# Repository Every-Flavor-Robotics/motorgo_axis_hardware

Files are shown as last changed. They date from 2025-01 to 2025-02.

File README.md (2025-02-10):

# MotorGo AXIS
## The aim of this project is to integrate a dual bldc motor controller with an ESP32 AND make it piHat compatible for the rpi 4 and 5
### Schematics and Layouts and Renders: 
(This is a first pass draft, so be patient with my formatting and content)

- Full board 3D:


- Top level


- Motor drivers 


- IMU 


- Power system 


- connectors 


- Dimensions 


## Demo
This is still in testing, but already at this state, it is capable of making 2 axis gantry robots quite easily.  Check out this project we made with it while developing the motor controller:
https://www.youtube.com/watch?v=p4cUWCG7fM4

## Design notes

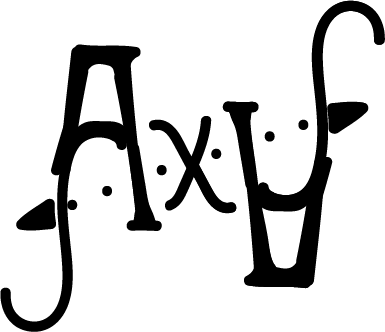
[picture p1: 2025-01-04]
graphics/1x/AxisArt.png

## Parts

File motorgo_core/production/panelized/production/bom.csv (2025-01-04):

Designator | Footprint | Quantity | Value | LCSC Part #
C1_3, C1_2, C1 | 0201 | 3 | 68pf 10v
C10_3, C10_2, C10, C11_3, C11_2, C11, C12_3, C12_2, C12, C13_3, C13_2, C13, C14_3, C14_2, C14, C21_3, C21_2, C21, C27_3, C27_2, C27, C28_3, C28_2, C28, C35_3, C35_2, C35, C36_3, C36_2, C36, C37_3, C37_2, C37, C38_3, C38_2, C38, C40_3, C40_2, C40, C41_3, C41_2, C41, C42_3, C42_2, C42, C43_3, C43_2, C43, C44_3, C44_2, C44, C45_3, C45_2, C45, C47_3, C47_2, C47, C48_3, C48_2, C48, C5_3, C5_2, C5, C6_3, C6_2, C6, C7_3, C7_2, C7, C8_3, C8_2, C8 | 0402 | 72 | 22uF 10v
C15_3, C15_2, C15, C2_3, C2_2, C2 | 0805 | 6 | 4.7uF 1mOhm 25v
C16_3, C16_2, C16 | CP_Elec_10x10.5 | 3 | 470uF 35V
C17_3, C17_2, C17 | 0603 | 3 | 4.7uF 1mOhm
C18_3, C18_2, C18 | 0201 | 3 | 2.2nF 0Ohm
C19_3, C19_2, C19 | 0805 | 3 | 4.7uF 1mOhm
C20_3, C20_2, C20 | 0201 | 3 | 6.8nf 10v
C22_3, C22_2, C22 | 0402 | 3 | 100nf 280mOhm
C23_3, C23_2, C23 | 1210 | 3 | 47uF 3mOhm 25v
C24_3, C24_2, C24, C25_3, C25_2, C25 | 0603 | 6 | 22uF 16v
C26_3, C26_2, C26, C30_3, C30_2, C30, C31_3, C31_2, C31, C34_3, C34_2, C34, C39_3, C39_2, C39, C4_3, C4_2, C4, C46_3, C46_2, C46, C9_3, C9_2, C9 | 0201 | 24 | 100nF 10v
C3_3, C3_2, C3, C33_3, C33_2, C33 | 0201 | 6 | 100nF 25v
C32_3, C32_2, C32 | 0603 | 3 | 1uF 10v
D1_3, D1_2, D1 | 0805 | 3 | LED blue
D10_3, D10_2, D10, D5_3, D5_2, D5, D6_3, D6_2, D6, D7_3, D7_2, D7, D8_3, D8_2, D8, D9_3, D9_2, D9 | B5819WS_SOD-323 | 18 | D_Schottky C7420331
D2_3, D2_2, D2 | 0805 | 3 | LED green
D3_3, D3_2, D3 | 0805 | 3 | LED red
D4_3, D4_2, D4 | TO-277_3P-L5.4-W4.0-LS6.5-TR | 3 | Schottky_SB1045L_C908747
J1_3, J1_2, J1 | USB-C-SMD_TYPEC-303-ACP16 | 3 | USB4520-03-0-A_REVA
J11_3, J11_2, J11 | CONN-TH_XT30PW-M | 3 | xt30
J13_3, J13_2, J13, J15_3, J15_2, J15 | JST_SH_BM04B-SRSS-TB_1x04-1MP_P1.00mm_Vertical | 6 | I2C_STANDARDQWIIC
J16_3, J16_2, J16, J18_3, J18_2, J18 | JST_SH_BM05B-SRSS-TB_1x05-1MP_P1.00mm_Vertical | 6 | BM05B-SRSS-TB_LF__SN_
J2_3, J2_2, J2, J3_3, J3_2, J3 | SW_SPST_TL3342 | 6 | C2886897
J4_3, J4_2, J4, J7_3, J7_2, J7 | PinSocket_2x20_P2.54mm_Vertical_SMD | 6 | Conn_02x20_Odd_Even
KIKIT_FID_B_1, KIKIT_FID_B_2, KIKIT_FID_B_3, KIKIT_FID_B_4, KIKIT_FID_T_1, KIKIT_FID_T_2, KIKIT_FID_T_3, KIKIT_FID_T_4 | Fiducial | 8 | Fiducial
KIKIT_TO_1, KIKIT_TO_2, KIKIT_TO_3, KIKIT_TO_4 | NPTH | 4 | NPTH
L1_3, L1_2, L1 | IND-SMD_L6.6-W6.4_CKSTT0610 | 3 | 2.2uH 12.7mOhm C5440776
Q1_3, Q1_2, Q1, Q10_3, Q10_2, Q10, Q11_3, Q11_2, Q11, Q12_3, Q12_2, Q12, Q2_3, Q2_2, Q2, Q3_3, Q3_2, Q3, Q4_3, Q4_2, Q4, Q5_3, Q5_2, Q5, Q6_3, Q6_2, Q6, Q7_3, Q7_2, Q7, Q8_3, Q8_2, Q8, Q9_3, Q9_2, Q9 | AP30H80Q_DFN-8 | 36 | AP30H80Q
R1_3, R1_2, R1, R2_3, R2_2, R2, R3_3, R3_2, R3, R46_3, R46_2, R46, R49_3, R49_2, R49, R50_3, R50_2, R50 | 0402 | 18 | 1k
R10_3, R10_2, R10, R11_3, R11_2, R11, R12_3, R12_2, R12, R13_3, R13_2, R13, R14_3, R14_2, R14, R15_3, R15_2, R15, R20_3, R20_2, R20, R21_3, R21_2, R21, R22_3, R22_2, R22, R23_3, R23_2, R23, R26_3, R26_2, R26, R27_3, R27_2, R27 | 0402 | 36 | 2R2
R16_3, R16_2, R16 | 0402 | 3 | 102k
R17_3, R17_2, R17 | 0402 | 3 | 36.5k
R18_3, R18_2, R18, R24_3, R24_2, R24 | 0402 | 6 | 53.6k
R19_3, R19_2, R19 | 0402 | 3 | 3.92k
R25_3, R25_2, R25 | 0402 | 3 | 10k
R30_3, R30_2, R30, R31_3, R31_2, R31, R32_3, R32_2, R32, R33_3, R33_2, R33, R4_3, R4_2, R4, R5_3, R5_2, R5, R8_3, R8_2, R8, R9_3, R9_2, R9 | 0402 | 24 | 5k1
R38_3, R38_2, R38, R39_3, R39_2, R39 | 0402 | 6 | 2k
R6_3, R6_2, R6, R7_3, R7_2, R7 | 0402 | 6 | 0
U1_3, U1_2, U1 | ESP32-S3-WROOM-1 | 3 | ESP32-S3-WROOM-1
U10_3, U10_2, U10 | LIS3MDLTR_LGA-12 | 3 | LIS3MDLTR
U11_3, U11_2, U11 | LSM6DSOTR_LGA-14 | 3 | LSM6DS3TR
U2_3, U2_2, U2 | SOT-666 | 3 | USBLC6-2P6
U3_3, U3_2, U3, U4_3, U4_2, U4 | FD6288Q_QFN-24 | 6 | FD6288
U6_3, U6_2, U6 | VQFN-14_L3.5-W3.5-P0.50-TL-EP_TPS54622RHLT | 3 | TPS54620RHLR
U8_3, U8_2, U8 | SOT-223-3_TabPin2 | 3 | AMS1117-3.3

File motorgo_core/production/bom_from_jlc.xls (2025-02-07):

Comment | topDesignator | bottomDesignator | Footprint | JLCPCB Part #
22uF10v | C10_3,C10_2,C10,C11_3,C11_2,C11,C12_3,C12_2,C12,C13_3,C13_2,C13,C14_3,C14_2,C14,C21_3,C21_2,C21,C27_3,C27_2,C27,C28_3,C28_2,C28,C35_3,C35_2,C35,C36_3,C36_2,C36,C37_3,C37_2,C37,C38_3,C38_2,C38,C40_3,C40_2,C40,C41_3,C41_2,C41,C42_3,C42_2,C42,C43_3,C43_2,C43,C44_3,C44_2,C44,C45_3,C45_2,C45,C47_3,C47_2,C47,C48_3,C48_2,C48,C5_3,C5_2,C5,C6_3,C6_2,C6,C7_3,C7_2,C7,C8_3,C8_2,C8 |  | 0402 | C3845593
22uF16v | C24_3,C24_2,C24,C25_3,C25_2,C25 |  | 0603 | C2762594
68pf10v | C1_3,C1_2,C1 |  | 0201 | C277473
4.7uF1mOhm | C15_3,C15_2,C15,C2_3,C2_2,C2,C19_3,C19_2,C19 |  | 0805 | C1779
FD6288 | U3_3,U3_2,U3,U4_3,U4_2,U4 |  | FD6288Q_QFN-24 | C328453
47uF3mOhm25v | C23_3,C23_2,C23 |  | 1210 | C7432791
10k | R25_3,R25_2,R25 |  | 0402 | C25744
6.8nf10v | C20_3,C20_2,C20 |  | 0201 | C565541
36.5k | R17_3,R17_2,R17 |  | 0402 | C25887
AP30H80Q | Q1_3,Q1_2,Q1,Q10_3,Q10_2,Q10,Q11_3,Q11_2,Q11,Q12_3,Q12_2,Q12,Q2_3,Q2_2,Q2,Q3_3,Q3_2,Q3,Q4_3,Q4_2,Q4,Q5_3,Q5_2,Q5,Q6_3,Q6_2,Q6,Q7_3,Q7_2,Q7,Q8_3,Q8_2,Q8,Q9_3,Q9_2,Q9 |  | AP30H80Q_DFN-8 | C2828592
TPS54620RHLR | U6_3,U6_2,U6 |  | VQFN-14_L3.5-W3.5-P0.50-TL-EP_TPS54622RHLT | C263274
USBLC6-2P6 | U2_3,U2_2,U2 |  | SOT-666 | C2827693
xt30 | J11_3,J11_2,J11 |  | CONN-TH_XT30PW-M | C431092
LSM6DS3TR | U11_3,U11_2,U11 |  | LSM6DSOTR_LGA-14 | C95230
LEDblue | D1_3,D1_2,D1 |  | 0805 | C2293
C2886897 | J2_3,J2_2,J2,J3_3,J3_2,J3 |  | SW_SPST_TL3342 | C2886897
2.2nF0Ohm | C18_3,C18_2,C18 |  | 0201 | C161488
4.7uF1mOhm | C17_3,C17_2,C17 |  | 0603 | C19666
BM05B-SRSS-TB_LF__SN_ | J16_3,J16_2,J16,J18_3,J18_2,J18 |  | JST_SH_BM05B-SRSS-TB_1x05-1MP_P1.00mm_Vertical | C160391
ESP32-S3-WROOM-1 | U1_3,U1_2,U1 |  | ESP32-S3-WROOM-1 | C2913202
LEDgreen | D2_3,D2_2,D2 |  | 0805 | C2297
1k | R1_3,R1_2,R1,R2_3,R2_2,R2,R3_3,R3_2,R3,R46_3,R46_2,R46,R49_3,R49_2,R49,R50_3,R50_2,R50 |  | 0402 | C11702
LEDred | D3_3,D3_2,D3 |  | 0805 | C434431
2.2uH12.7mOhmC5440776 | L1_3,L1_2,L1 |  | IND-SMD_L6.6-W6.4_CKSTT0610 | C5440776
100nF25v | C26_3,C26_2,C26,C30_3,C30_2,C30,C31_3,C31_2,C31,C34_3,C34_2,C34,C39_3,C39_2,C39,C4_3,C4_2,C4,C46_3,C46_2,C46,C9_3,C9_2,C9,C3_3,C3_2,C3,C33_3,C33_2,C33 |  | 0201 | C76939
3.92k | R19_3,R19_2,R19 |  | 0402 | C137988
100nf280mOhm | C22_3,C22_2,C22 |  | 0402 | C1525
5k1 | R30_3,R30_2,R30,R31_3,R31_2,R31,R32_3,R32_2,R32,R33_3,R33_2,R33,R4_3,R4_2,R4,R5_3,R5_2,R5,R8_3,R8_2,R8,R9_3,R9_2,R9 |  | 0402 | C25905
2k | R38_3,R38_2,R38,R39_3,R39_2,R39 |  | 0402 | C4109
53.6k | R18_3,R18_2,R18,R24_3,R24_2,R24 |  | 0402 | C53398
USB4520-03-0-A_REVA | J1_3,J1_2,J1 |  | USB-C-SMD_TYPEC-303-ACP16 | C720628
Conn_02x20_Odd_Even | J4_3,J4_2,J4 | J7_3,J7_2,J7 | PinSocket_2x20_P2.54mm_Vertical_SMD | C3975165
D_SchottkyC7420331 | D10_3,D10_2,D10,D5_3,D5_2,D5,D6_3,D6_2,D6,D7_3,D7_2,D7,D8_3,D8_2,D8,D9_3,D9_2,D9 |  | B5819WS_SOD-323 | C7420331
102k | R16_3,R16_2,R16 |  | 0402 | C26991
LIS3MDLTR | U10_3,U10_2,U10 |  | LIS3MDLTR_LGA-12 | C478483
470uF35V | C16_3,C16_2,C16 |  | CP_Elec_10x10.5 | C2836436
0 | R6_3,R6_2,R6,R7_3,R7_2,R7 |  | 0402 | C17168
1uF10v | C32_3,C32_2,C32 |  | 0603 | C15849
AMS1117-3.3 | U8_3,U8_2,U8 |  | SOT-223-3_TabPin2 | C6186
I2C_STANDARDQWIIC | J13_3,J13_2,J13,J15_3,J15_2,J15 |  | JST_SH_BM04B-SRSS-TB_1x04-1MP_P1.00mm_Vertical | C160390
2R2 | R10_3,R10_2,R10,R11_3,R11_2,R11,R12_3,R12_2,R12,R13_3,R13_2,R13,R14_3,R14_2,R14,R15_3,R15_2,R15,R20_3,R20_2,R20,R21_3,R21_2,R21,R22_3,R22_2,R22,R23_3,R23_2,R23,R26_3,R26_2,R26,R27_3,R27_2,R27 |  | 0402 | C25158
Schottky_SB1045L_C908747 | D4_3,D4_2,D4 |  | TO-277_3P-L5.4-W4.0-LS6.5-TR | C908747

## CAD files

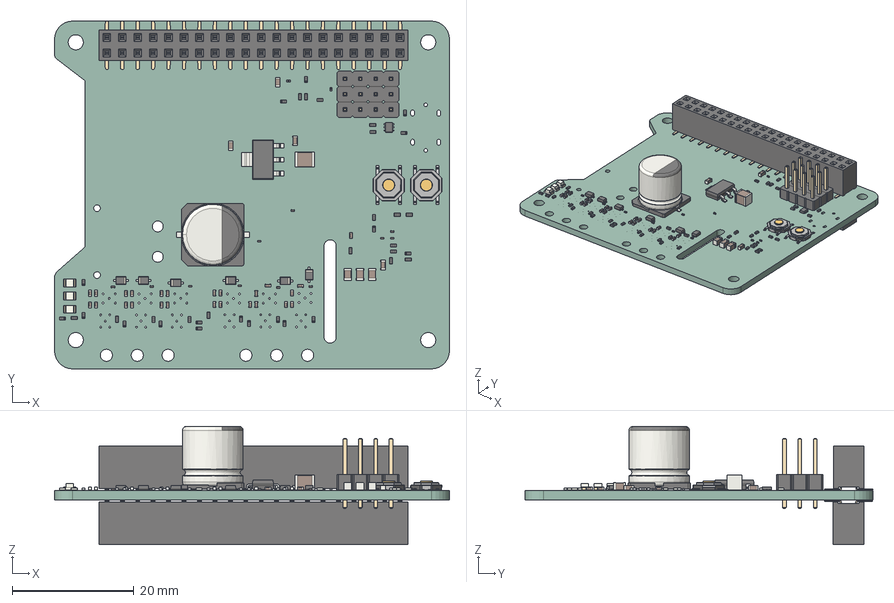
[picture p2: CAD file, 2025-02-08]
mg_axis.step
65.0 x 57.2 x 19.5 mm
C_0402_1005Metric x 25
C_0201_0603Metric x 13
R_0402_1005Metric x 36
D_SOD_323F x 6
SW_SPST_TL3342 x 2
C_0603_1608Metric x 4
PinHeader_1x04_P254mm_Vertical x 3
SOT_666
LED_0805_2012Metric x 3
C_0805_2012Metric x 3
CP_Elec_10x105
SOT_223
C_1210_3225Metric
PinSocket_2x20_P254mm_Vertical_SMD x 2
motorgo_core_PCB

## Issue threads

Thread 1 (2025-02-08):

3D model is missing parts

alexchunlin, 2025-02-08:
## Currently, the 3d STEP file of the board has the biggest components, like the board outline, the bulk capacitor, and the GPIO headers for the top and bottom of the board.

### HOWEVER it is still missing the following big components:
- esp32
- USBC port
- Qwiic ports
- Encoder ports
- XT30 Connector

### As wells as the following smaller components that people might care about:
- mosfets
- leds
- literally every SMD passive, but particularly the chonky inductor
- the IMU and Magnetometer

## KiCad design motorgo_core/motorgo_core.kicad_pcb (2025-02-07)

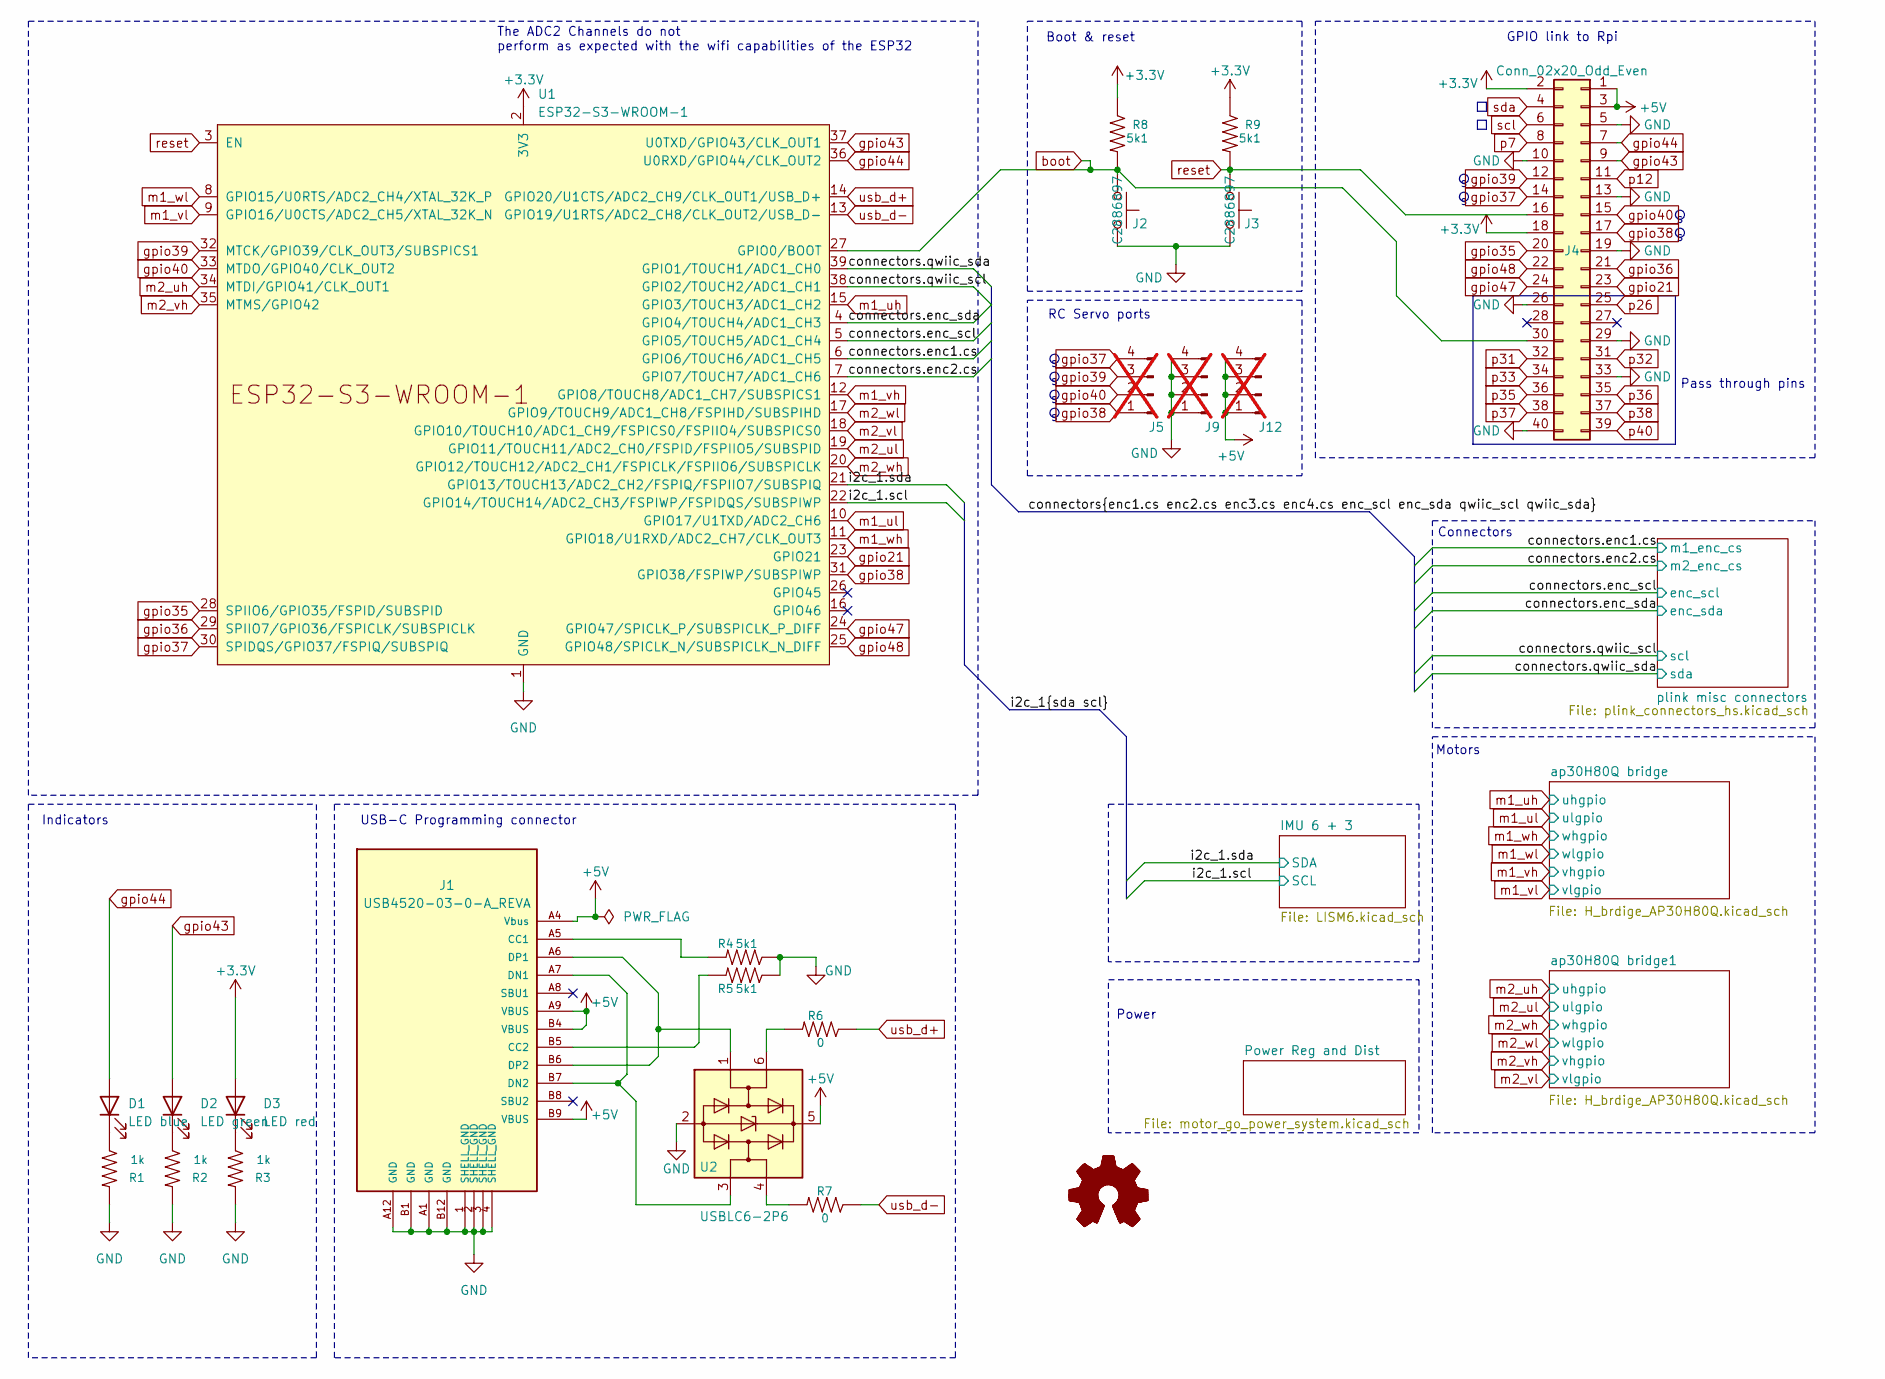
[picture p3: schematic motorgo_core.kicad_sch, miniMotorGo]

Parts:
D1: LED blue; LED_0805_2012Metric; LCSC_Part_Number C84259
D2: LED green; LED_0805_2012Metric; LCSC_Part_Number C84260
D3: LED red; LED_0805_2012Metric; LCSC_Part_Number C84256
J1: USB4520-03-0-A_REVA; USB-C-SMD_TYPEC-303-ACP16; LCSC_Part_Number C720628
J2, J3: C2886897; SW_SPST_TL3342; LCSC_Part_Number C2886897
J4: Conn_02x20_Odd_Even; PinSocket_2x20_P2.54mm_Vertical_SMD; LCSC_Part_Number C3975165
J5, J9, J12: Conn_01x04_Pin; PinHeader_1x04_P2.54mm_Vertical; not fitted
R1, R2, R3: 1k; R_0402_1005Metric; LCSC_Part_Number C11702
R4, R5, R8, R9: 5k1; R_0402_1005Metric; LCSC_Part_Number C25905
R6, R7: 0; R_0402_1005Metric; LCSC_Part_Number C3017451
U1: ESP32-S3-WROOM-1; LCSC_Part_Number C2913198
U2: USBLC6-2P6; SOT-666; LCSC_Part_Number C2827693

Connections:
+3.3V: D3.2 (A), J4.2, J4.18, R8.1, R9.1, U1.2 (3V3); also elsewhere on the board
+5V: J1.A4 (Vbus), J1.A9 (VBUS), J1.B4 (VBUS), J1.B9 (VBUS), J4.1, J4.3, J12.1, J12.2, J12.3, J12.4, U2.5 (VBUS); also elsewhere on the board
/connectors.enc1.cs: U1.6 (GPIO6/TOUCH6/ADC1_CH5); also elsewhere on the board
/connectors.enc2.cs: U1.7 (GPIO7/TOUCH7/ADC1_CH6); also elsewhere on the board
/connectors.enc_scl: U1.5 (GPIO5/TOUCH5/ADC1_CH4); also elsewhere on the board
/connectors.enc_sda: U1.4 (GPIO4/TOUCH4/ADC1_CH3); also elsewhere on the board
/i2c_1.scl: U1.22 (GPIO14/TOUCH14/ADC2_CH3/FSPIWP/FSPIDQS/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); also elsewhere on the board
/i2c_1.sda: U1.21 (GPIO13/TOUCH13/ADC2_CH2/FSPIQ/FSPIIO7/S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); also elsewhere on the board
GND: J1.1 (SHELL_GND), J1.2 (SHELL_GND), J1.3 (SHELL_GND), J1.4 (SHELL_GND), J1.A1 (GND), J1.A12 (GND), J1.B1 (GND), J1.B12 (GND), J2.1, J3.2, J4.5, J4.10, J4.13, J4.19, J4.26, J4.29, J4.33, J4.40, J9.1, J9.2, J9.3, J9.4, R1.2, R2.2, R3.2, R4.1, R5.1, U1.1 (GND), U1.40 (GND), U1.41 (GND), U2.2 (GND); also elsewhere on the board
unnamed: D1.1 (K), R1.1
unnamed: D2.1 (K), R2.1
unnamed: D3.1 (K), R3.1
unnamed: J1.A5 (CC1), R4.2
unnamed: J1.B5 (CC2), R5.2
unnamed: J1.A7 (DN1), J1.B7 (DN2), U2.3 (I/O2)
unnamed: J1.A6 (DP1), J1.B6 (DP2), U2.1 (I/O1)
unnamed: R6.2, U2.6 (I/O1)
unnamed: R7.2, U2.4 (I/O2)
boot: J2.2, J4.30, R8.2, U1.27 (GPIO0/BOOT); also elsewhere on the board
gpio21: J4.23, U1.23 (GPIO21); also elsewhere on the board
gpio35: J4.20, U1.28 (SPIIO6/GPIO35/FSPID/SUBSPID); also elsewhere on the board
gpio36: J4.21, U1.29 (SPIIO7/GPIO36/FSPICLK/SUBSPICLK); also elsewhere on the board
gpio37: J4.14, J5.4, U1.30 (SPIDQS/GPIO37/FSPIQ/SUBSPIQ); also elsewhere on the board
gpio38: J4.17, J5.1, U1.31 (GPIO38/FSPIWP/SUBSPIWP); also elsewhere on the board
gpio39: J4.12, J5.3, U1.32 (MTCK/GPIO39/CLK_OUT3/SUBSPICS1); also elsewhere on the board
gpio40: J4.15, J5.2, U1.33 (MTDO/GPIO40/CLK_OUT2); also elsewhere on the board
gpio43: D2.2 (A), J4.9, U1.37 (U0TXD/GPIO43/CLK_OUT1); also elsewhere on the board
gpio44: D1.2 (A), J4.7, U1.36 (U0RXD/GPIO44/CLK_OUT2); also elsewhere on the board
gpio47: J4.24, U1.24 (GPIO47/SPICLK_P/SUBSPICLK_P_DIFF); also elsewhere on the board
gpio48: J4.22, U1.25 (GPIO48/SPICLK_N/SUBSPICLK_N_DIFF); also elsewhere on the board
m1_uh: U1.15 (GPIO3/TOUCH3/ADC1_CH2); also elsewhere on the board
m1_ul: U1.10 (GPIO17/U1TXD/ADC2_CH6); also elsewhere on the board
m1_vh: U1.12 (GPIO8/TOUCH8/ADC1_CH7/SUBSPICS1); also elsewhere on the board
m1_vl: U1.9 (GPIO16/U0CTS/ADC2_CH5/XTAL_32K_N); also elsewhere on the board
m1_wh: U1.11 (GPIO18/U1RXD/ADC2_CH7/CLK_OUT3); also elsewhere on the board
m1_wl: U1.8 (GPIO15/U0RTS/ADC2_CH4/XTAL_32K_P); also elsewhere on the board
m2_uh: U1.34 (MTDI/GPIO41/CLK_OUT1); also elsewhere on the board
m2_ul: U1.19 (GPIO11/TOUCH11/ADC2_CH0/FSPID/FSPIIO5/S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); also elsewhere on the board
m2_vh: U1.35 (MTMS/GPIO42); also elsewhere on the board
m2_vl: U1.18 (GPIO10/TOUCH10/ADC1_CH9/FSPICS0/FSPIIO4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); also elsewhere on the board
m2_wh: U1.20 (GPIO12/TOUCH12/ADC2_CH1/FSPICLK/FSPIIO6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); also elsewhere on the board
m2_wl: U1.17 (GPIO9/TOUCH9/ADC1_CH8/FSPIHD/SUBSPIHD); also elsewhere on the board
p7: J4.8; also elsewhere on the board
p12: J4.11; also elsewhere on the board
p26: J4.25; also elsewhere on the board
p31: J4.32; also elsewhere on the board
p32: J4.31; also elsewhere on the board
p33: J4.34; also elsewhere on the board
p35: J4.36; also elsewhere on the board
p36: J4.35; also elsewhere on the board
p37: J4.38; also elsewhere on the board
p38: J4.37; also elsewhere on the board
p40: J4.39; also elsewhere on the board
reset: J3.1, J4.16, R9.2, U1.3 (EN); also elsewhere on the board
scl: J4.6, U1.38 (GPIO2/TOUCH2/ADC1_CH1); also elsewhere on the board
sda: J4.4, U1.39 (GPIO1/TOUCH1/ADC1_CH0); also elsewhere on the board
usb_d+: R6.1, U1.14 (GPIO20/U1CTS/ADC2_CH9/CLK_OUT1/USB_D+)
usb_d-: R7.1, U1.13 (GPIO19/U1RTS/ADC2_CH8/CLK_OUT2/USB_D-)

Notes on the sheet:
USB-C Programming connector
Motors
Power
Boot & reset
Indicators
The ADC2 Channels do not perform as expected with the wifi capabilities of the ESP32
Pass through pins
Connectors
RC Servo ports
GPIO link to Rpi

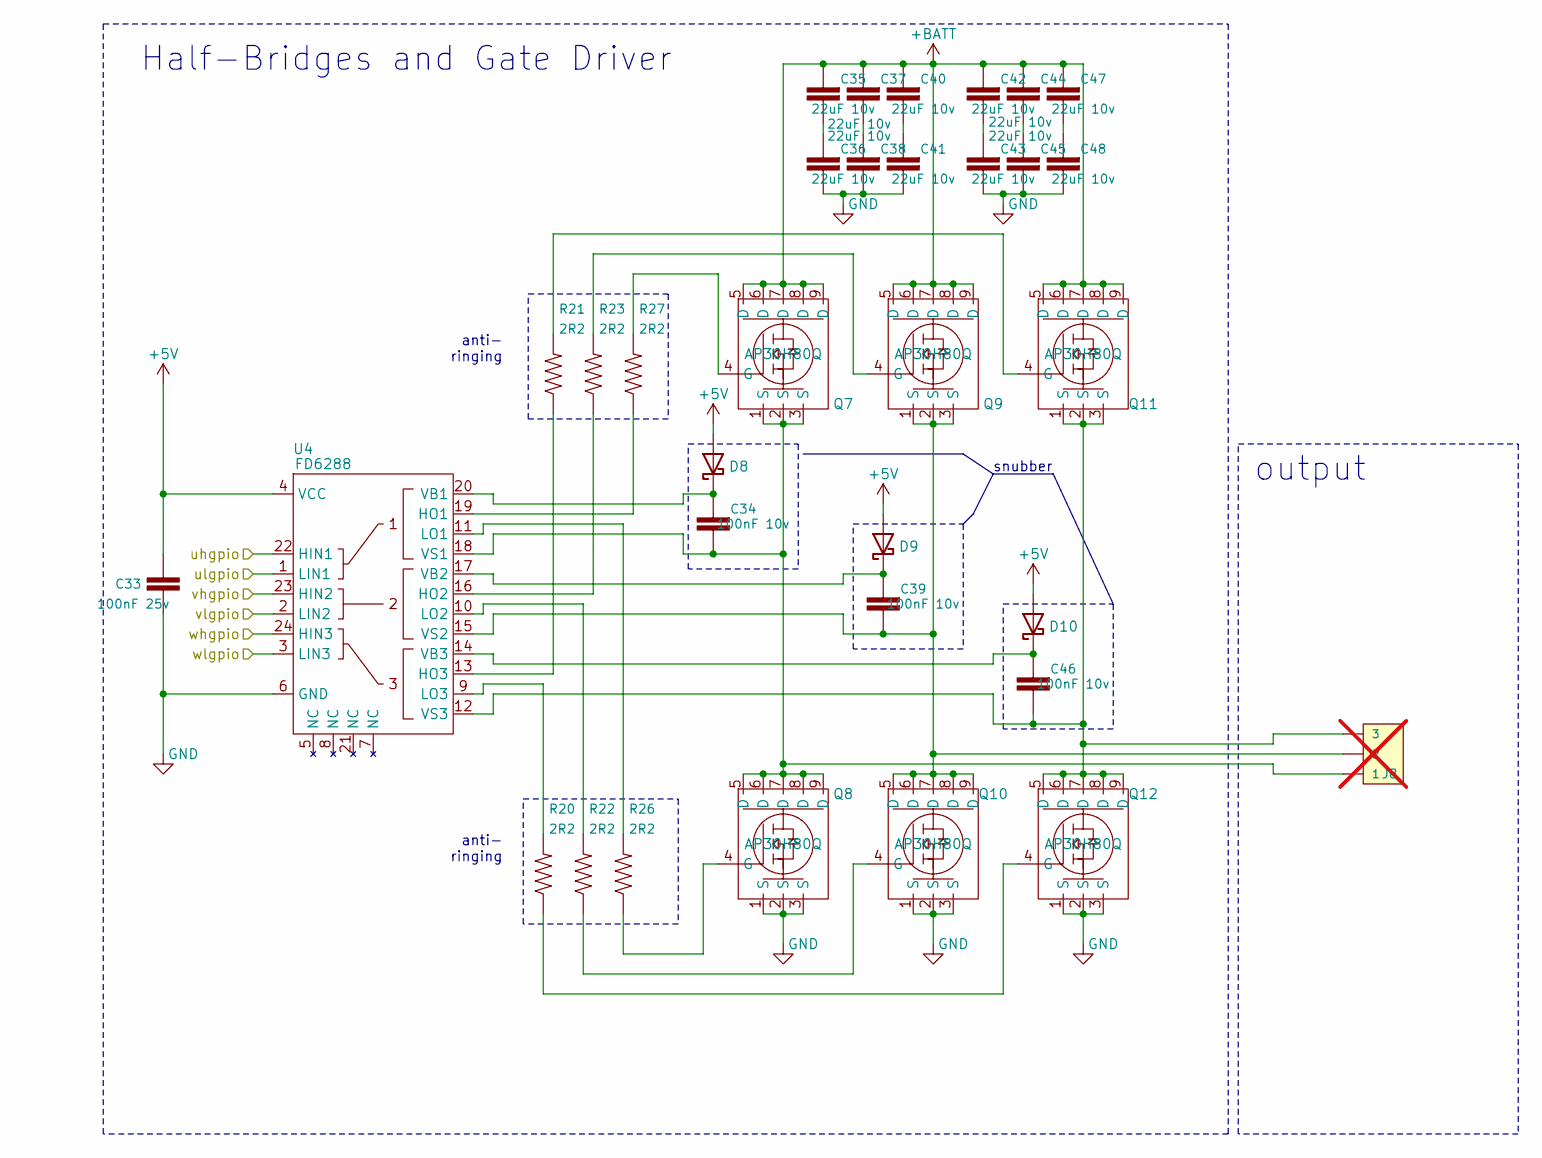
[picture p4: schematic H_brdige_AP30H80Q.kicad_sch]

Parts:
C33: 100nF 25v; C_0201_0603Metric; Manufacturer_Part_Number CC0402KRX7R7BB104; LCSC_Part_Number C60474
C34, C39, C46: 100nF 10v; C_0201_0603Metric; Manufacturer_Part_Number CC0402KRX7R7BB104; LCSC_Part_Number C60474
C35, C36, C37, C38, C40, C41, C42, C43, C44, C45, C47, C48: 22uF 10v; C_0402_1005Metric; LCSC_Part_Number C3845593
D8, D9, D10: D_Schottky C7420331; B5819WS_SOD-323; LCSC_Part_Number C7420331
J8: DNP; 3 phase motor; not fitted
Q7, Q8, Q9, Q10, Q11, Q12: AP30H80Q; AP30H80Q_DFN-8; LCSC_Part_Number C2828592
R20, R21, R22, R23, R26, R27: 2R2; R_0402_1005Metric; LCSC_Part_Number C25158
U4: FD6288; FD6288Q_QFN-24; LCSC_Part_Number C328453

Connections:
+5V: C33.1, D8.2 (A), D9.2 (A), D10.2 (A), U4.4 (VCC); also elsewhere on the board
+BATT: C35.2, C37.2, C40.2, C42.2, C44.2, C47.2, Q7.5 (D), Q7.6 (D), Q7.7 (D), Q7.8 (D), Q7.9 (D), Q9.5 (D), Q9.6 (D), Q9.7 (D), Q9.8 (D), Q9.9 (D), Q11.5 (D), Q11.6 (D), Q11.7 (D), Q11.8 (D), Q11.9 (D); also elsewhere on the board
GND: C33.2, C36.1, C38.1, C41.1, C43.1, C45.1, C48.1, Q8.1 (S), Q8.2 (S), Q8.3 (S), Q10.1 (S), Q10.2 (S), Q10.3 (S), Q12.1 (S), Q12.2 (S), Q12.3 (S), U4.6 (GND); also elsewhere on the board
unnamed: C35.1, C36.2
unnamed: C37.1, C38.2
unnamed: C40.1, C41.2
unnamed: C42.1, C43.2
unnamed: C44.1, C45.2
unnamed: C47.1, C48.2
unnamed: C34.2, D8.1 (K), U4.20 (VB1)
unnamed: C39.2, D9.1 (K), U4.17 (VB2)
unnamed: C46.2, D10.1 (K), U4.14 (VB3)
unnamed: Q7.4 (G), R27.2
unnamed: Q8.4 (G), R26.1
unnamed: Q9.4 (G), R23.2
unnamed: Q10.4 (G), R22.1
unnamed: Q11.4 (G), R21.2
unnamed: Q12.4 (G), R20.1
unnamed: R27.1, U4.19 (HO1)
unnamed: R23.1, U4.16 (HO2)
unnamed: R21.1, U4.13 (HO3)
unnamed: R26.2, U4.11 (LO1)
unnamed: R22.2, U4.10 (LO2)
unnamed: R20.2, U4.9 (LO3)
unnamed: C34.1, J8.1, Q7.1 (S), Q7.2 (S), Q7.3 (S), Q8.5 (D), Q8.6 (D), Q8.7 (D), Q8.8 (D), Q8.9 (D), U4.18 (VS1)
unnamed: C39.1, J8.2, Q9.1 (S), Q9.2 (S), Q9.3 (S), Q10.5 (D), Q10.6 (D), Q10.7 (D), Q10.8 (D), Q10.9 (D), U4.15 (VS2)
unnamed: C46.1, J8.3, Q11.1 (S), Q11.2 (S), Q11.3 (S), Q12.5 (D), Q12.6 (D), Q12.7 (D), Q12.8 (D), Q12.9 (D), U4.12 (VS3)
m2_uh: U4.22 (HIN1); also elsewhere on the board
m2_ul: U4.1 (LIN1); also elsewhere on the board
m2_vh: U4.23 (HIN2); also elsewhere on the board
m2_vl: U4.2 (LIN2); also elsewhere on the board
m2_wh: U4.24 (HIN3); also elsewhere on the board
m2_wl: U4.3 (LIN3); also elsewhere on the board

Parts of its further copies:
C3: 100nF 25v; C_0201_0603Metric; Manufacturer_Part_Number CC0402KRX7R7BB104; LCSC_Part_Number C60474
C4, C9, C26: 100nF 10v; C_0201_0603Metric; Manufacturer_Part_Number CC0402KRX7R7BB104; LCSC_Part_Number C60474
C5, C6, C7, C8, C10, C11, C12, C13, C14, C21, C27, C28: 22uF 10v; C_0402_1005Metric; LCSC_Part_Number C3845593
D5, D6, D7: D_Schottky C7420331; B5819WS_SOD-323; LCSC_Part_Number C7420331
J6: DNP; 3 phase motor; not fitted
Q1, Q2, Q3, Q4, Q5, Q6: AP30H80Q; AP30H80Q_DFN-8; LCSC_Part_Number C2828592
R10, R11, R12, R13, R14, R15: 2R2; R_0402_1005Metric; LCSC_Part_Number C25158
U3: FD6288; FD6288Q_QFN-24; LCSC_Part_Number C328453

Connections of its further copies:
+5V: C3.1, D5.2 (A), D6.2 (A), D7.2 (A), U3.4 (VCC); also elsewhere on the board
+BATT: C5.2, C7.2, C10.2, C12.2, C14.2, C27.2, Q1.5 (D), Q1.6 (D), Q1.7 (D), Q1.8 (D), Q1.9 (D), Q3.5 (D), Q3.6 (D), Q3.7 (D), Q3.8 (D), Q3.9 (D), Q5.5 (D), Q5.6 (D), Q5.7 (D), Q5.8 (D), Q5.9 (D); also elsewhere on the board
GND: C3.2, C6.1, C8.1, C11.1, C13.1, C21.1, C28.1, Q2.1 (S), Q2.2 (S), Q2.3 (S), Q4.1 (S), Q4.2 (S), Q4.3 (S), Q6.1 (S), Q6.2 (S), Q6.3 (S), U3.6 (GND); also elsewhere on the board
unnamed: C5.1, C6.2
unnamed: C7.1, C8.2
unnamed: C10.1, C11.2
unnamed: C12.1, C13.2
unnamed: C14.1, C21.2
unnamed: C27.1, C28.2
unnamed: C4.2, D5.1 (K), U3.20 (VB1)
unnamed: C9.2, D6.1 (K), U3.17 (VB2)
unnamed: C26.2, D7.1 (K), U3.14 (VB3)
unnamed: Q1.4 (G), R15.2
unnamed: Q2.4 (G), R14.1
unnamed: Q3.4 (G), R13.2
unnamed: Q4.4 (G), R12.1
unnamed: Q5.4 (G), R11.2
unnamed: Q6.4 (G), R10.1
unnamed: R15.1, U3.19 (HO1)
unnamed: R13.1, U3.16 (HO2)
unnamed: R11.1, U3.13 (HO3)
unnamed: R14.2, U3.11 (LO1)
unnamed: R12.2, U3.10 (LO2)
unnamed: R10.2, U3.9 (LO3)
unnamed: C4.1, J6.1, Q1.1 (S), Q1.2 (S), Q1.3 (S), Q2.5 (D), Q2.6 (D), Q2.7 (D), Q2.8 (D), Q2.9 (D), U3.18 (VS1)
unnamed: C9.1, J6.2, Q3.1 (S), Q3.2 (S), Q3.3 (S), Q4.5 (D), Q4.6 (D), Q4.7 (D), Q4.8 (D), Q4.9 (D), U3.15 (VS2)
unnamed: C26.1, J6.3, Q5.1 (S), Q5.2 (S), Q5.3 (S), Q6.5 (D), Q6.6 (D), Q6.7 (D), Q6.8 (D), Q6.9 (D), U3.12 (VS3)
m1_uh: U3.22 (HIN1); also elsewhere on the board
m1_ul: U3.1 (LIN1); also elsewhere on the board
m1_vh: U3.23 (HIN2); also elsewhere on the board
m1_vl: U3.2 (LIN2); also elsewhere on the board
m1_wh: U3.24 (HIN3); also elsewhere on the board
m1_wl: U3.3 (LIN3); also elsewhere on the board

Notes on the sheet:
output
anti- ringing
Half-Bridges and Gate Driver
snubber

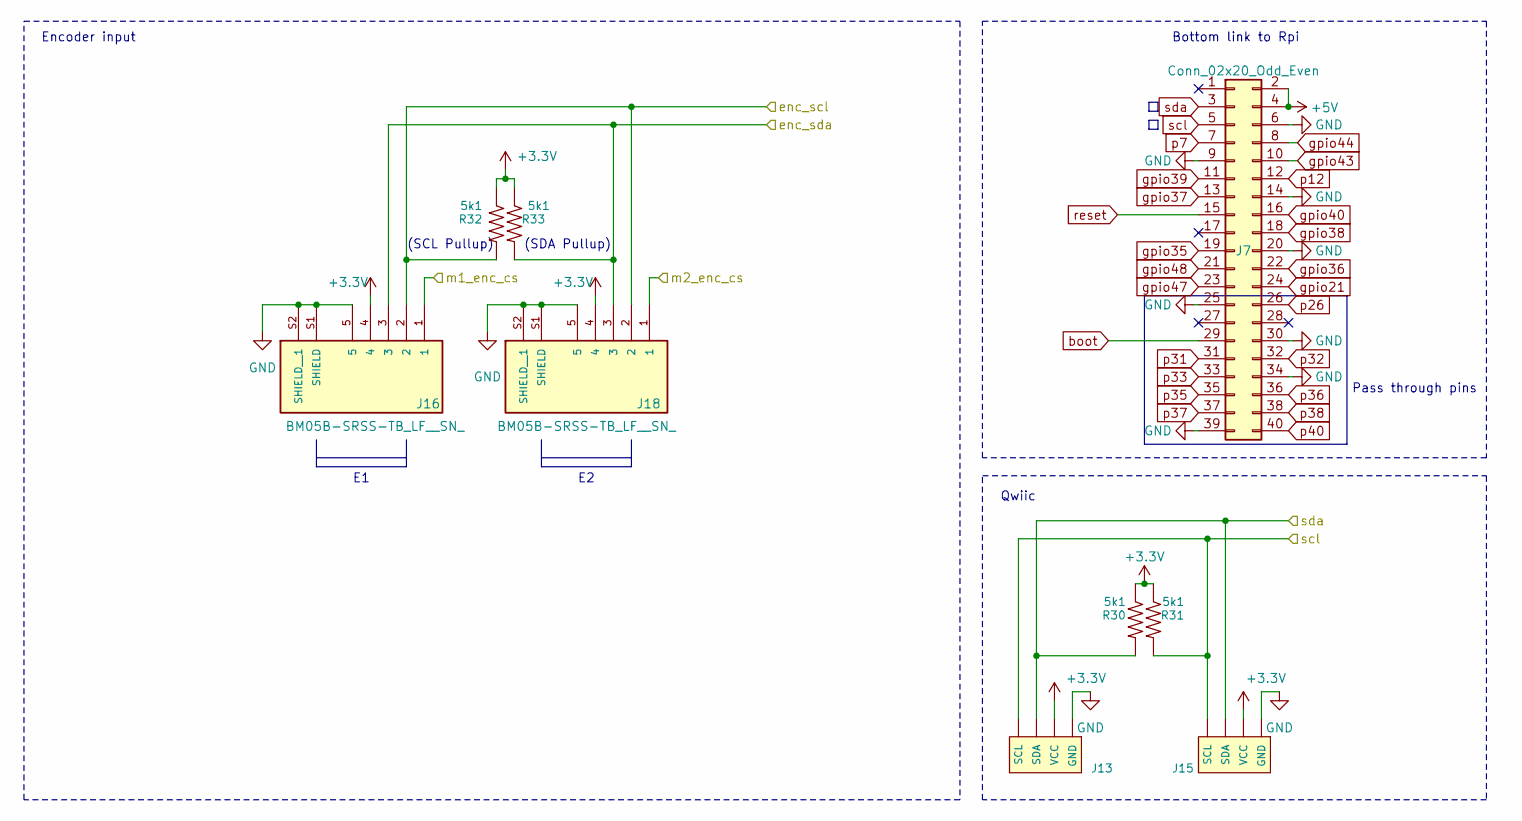
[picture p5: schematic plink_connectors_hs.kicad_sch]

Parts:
J7: Conn_02x20_Odd_Even; PinSocket_2x20_P2.54mm_Vertical_SMD; LCSC_Part_Number C3975165
J13, J15: I2C_STANDARDQWIIC; JST_SH_BM04B-SRSS-TB_1x04-1MP_P1.00mm_Vertical; LCSC_Part_Number C160404
J16, J18: BM05B-SRSS-TB_LF__SN_; JST_SH_BM05B-SRSS-TB_1x05-1MP_P1.00mm_Vertical; PARTREV N/A; LCSC_Part_Number C265092
R30, R31, R32, R33: 5k1; R_0402_1005Metric; LCSC_Part_Number C25905

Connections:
+3.3V: J13.2 (VCC), J15.2 (VCC), J16.4, J18.4, R30.1, R31.1, R32.1, R33.1; also elsewhere on the board
+5V: J7.2, J7.4; also elsewhere on the board
/connectors.enc1.cs: J16.1; also elsewhere on the board
/connectors.enc2.cs: J18.1; also elsewhere on the board
/connectors.enc_scl: J16.2, J18.2, R32.2; also elsewhere on the board
/connectors.enc_sda: J16.3, J18.3, R33.2; also elsewhere on the board
GND: J7.6, J7.9, J7.14, J7.20, J7.25, J7.30, J7.34, J7.39, J13.1 (GND), J15.1 (GND), J16.5, J16.S1 (SHIELD), J16.S2 (SHIELD__1), J18.5, J18.S1 (SHIELD), J18.S2 (SHIELD__1); also elsewhere on the board
boot: J7.29; also elsewhere on the board
gpio21: J7.24; also elsewhere on the board
gpio35: J7.19; also elsewhere on the board
gpio36: J7.22; also elsewhere on the board
gpio37: J7.13; also elsewhere on the board
gpio38: J7.18; also elsewhere on the board
gpio39: J7.11; also elsewhere on the board
gpio40: J7.16; also elsewhere on the board
gpio43: J7.10; also elsewhere on the board
gpio44: J7.8; also elsewhere on the board
gpio47: J7.23; also elsewhere on the board
gpio48: J7.21; also elsewhere on the board
p7: J7.7; also elsewhere on the board
p12: J7.12; also elsewhere on the board
p26: J7.26; also elsewhere on the board
p31: J7.31; also elsewhere on the board
p32: J7.32; also elsewhere on the board
p33: J7.33; also elsewhere on the board
p35: J7.35; also elsewhere on the board
p36: J7.36; also elsewhere on the board
p37: J7.37; also elsewhere on the board
p38: J7.38; also elsewhere on the board
p40: J7.40; also elsewhere on the board
reset: J7.15; also elsewhere on the board
scl: J7.5, J13.4 (SCL), J15.4 (SCL), R31.2; also elsewhere on the board
sda: J7.3, J13.3 (SDA), J15.3 (SDA), R30.2; also elsewhere on the board

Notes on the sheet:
Qwiic
Bottom link to Rpi
Encoder input
(SCL Pullup)
Pass through pins
(SDA Pullup)

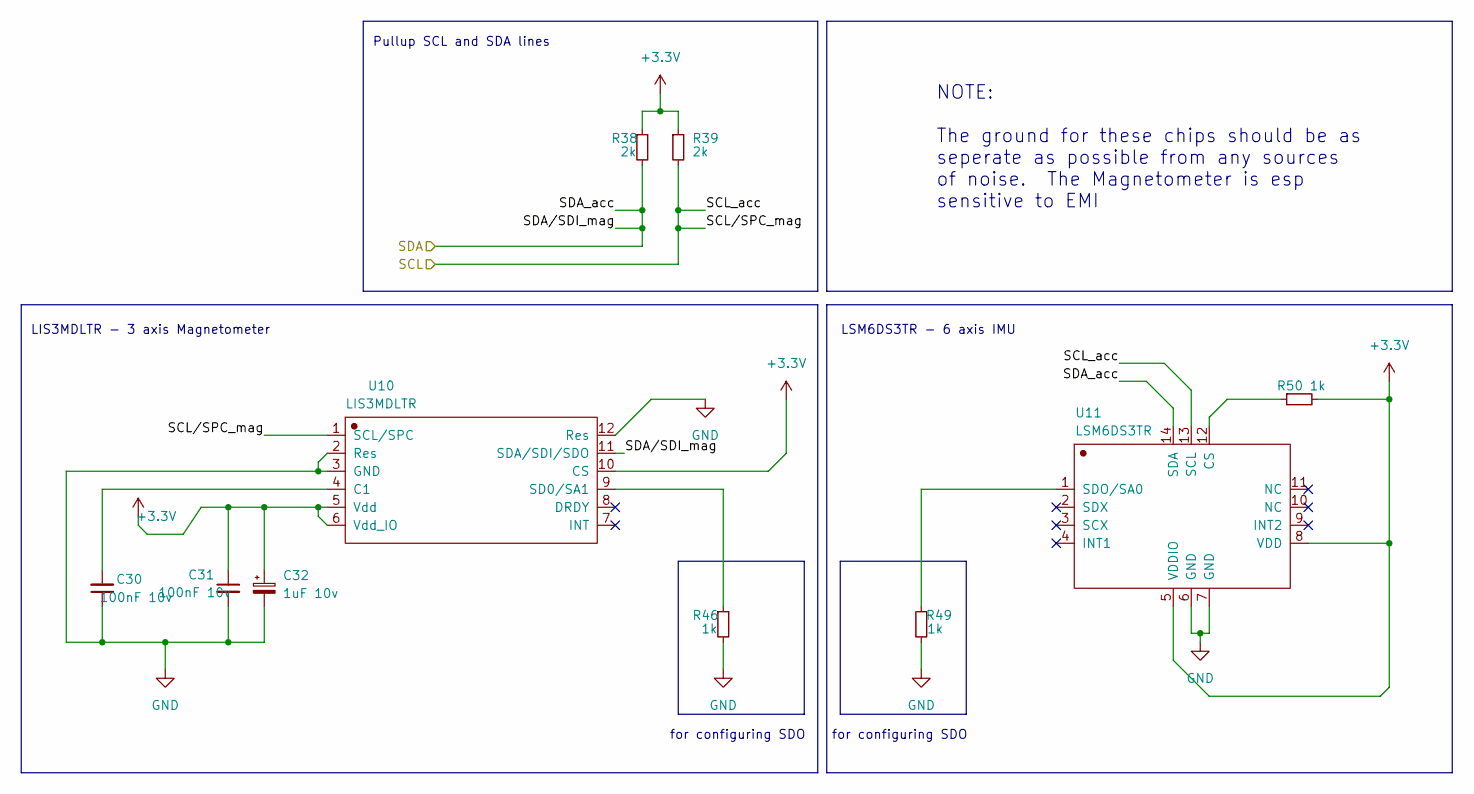
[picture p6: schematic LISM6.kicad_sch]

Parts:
C30, C31: 100nF 10v; C_0201_0603Metric; LCSC_Part_Number C880603
C32: 1uF 10v; C_0603_1608Metric; LCSC_Part_Number C15849
R38, R39: 2k; R_0402_1005Metric; LCSC_Part_Number C4109
R46, R49, R50: 1k; R_0402_1005Metric; LCSC_Part_Number C11702
U10: LIS3MDLTR; LIS3MDLTR_LGA-12; LCSC_Part_Number C478483
U11: LSM6DS3TR; LSM6DSOTR_LGA-14; LCSC_Part_Number C95230

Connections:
+3.3V: C31.1, C32.1, R38.1, R39.1, R50.2, U10.5 (Vdd), U10.6 (Vdd_IO), U10.10 (CS), U11.5 (VDDIO), U11.8 (VDD); also elsewhere on the board
/i2c_1.scl: R39.2, U10.1 (SCL/SPC), U11.13 (SCL); also elsewhere on the board
/i2c_1.sda: R38.2, U10.11 (SDA/SDI/SDO), U11.14 (SDA); also elsewhere on the board
GND: C30.1, C31.2, C32.2, R46.2, R49.2, U10.2 (Res), U10.3 (GND), U10.12 (Res), U11.6 (GND), U11.7 (GND); also elsewhere on the board
unnamed: C30.2, U10.4 (C1)
unnamed: R46.1, U10.9 (SD0/SA1)
unnamed: R50.1, U11.12 (CS)
unnamed: R49.1, U11.1 (SDO/SA0)

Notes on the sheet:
NOTE: The ground for these chips should be as seperate as possible from any sources of noise. The Magnetometer is esp sensitive to EMI
for configuring SDO
LSM6DS3TR - 6 axis IMU
Pullup SCL and SDA lines
LIS3MDLTR - 3 axis Magnetometer

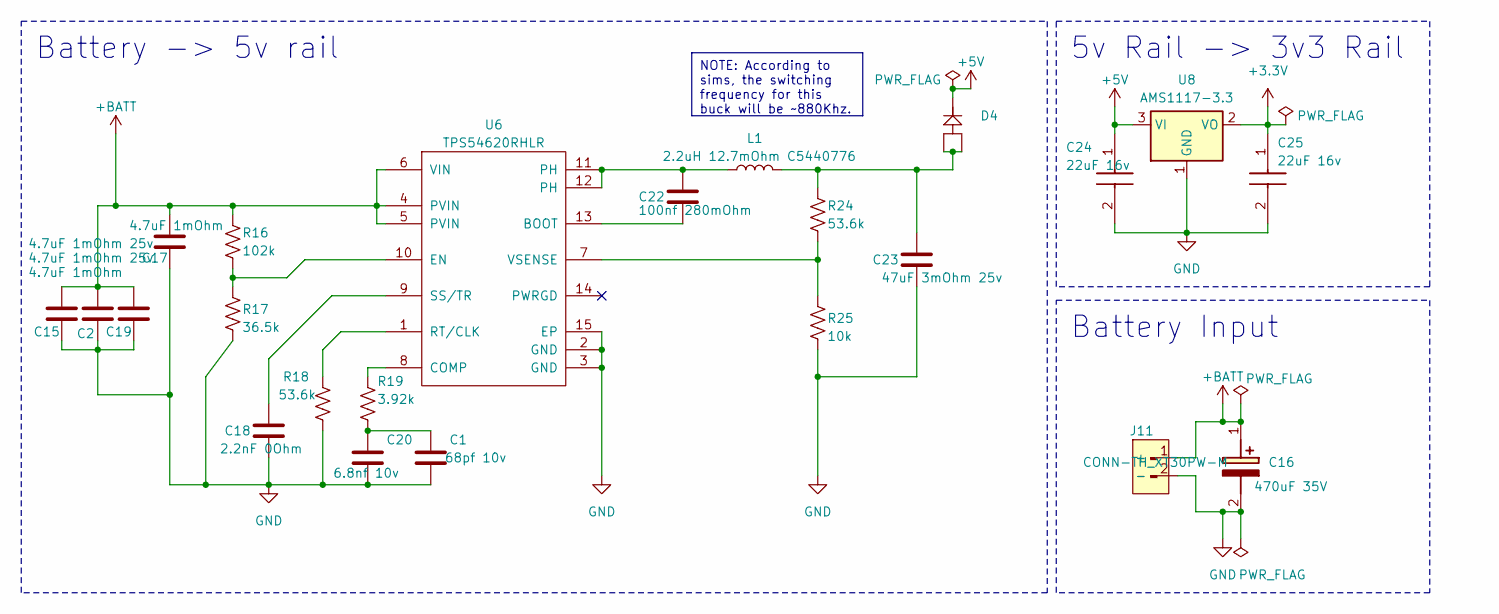
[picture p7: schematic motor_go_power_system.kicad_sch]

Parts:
C1: 68pf 10v; C_0201_0603Metric; LCSC_Part_Number C3037638
C2, C15: 4.7uF 1mOhm 25v; C_0805_2012Metric; LCSC_Part_Number C5448891
C16: 470uF 35V; CP_Elec_10x10.5; Mouser Part Number 140-RGA221M1EBK0811G
C17: 4.7uF 1mOhm; C_0603_1608Metric; LCSC_Part_Number C6119856
C18: 2.2nF 0Ohm; C_0201_0603Metric; LCSC_Part_Number C285033
C19: 4.7uF 1mOhm; C_0805_2012Metric; LCSC_Part_Number C5448891
C20: 6.8nf 10v; C_0201_0603Metric; LCSC_Part_Number C3037638
C22: 100nf 280mOhm; C_0402_1005Metric; LCSC_Part_Number C880603
C23: 47uF 3mOhm 25v; C_1210_3225Metric; LCSC_Part_Number C7432791
C24, C25: 22uF 16v; C_0603_1608Metric; Mouser Part Number 187-CL21A226MQQNNNE
D4: Schottky_SB1045L_C908747; TO-277_3P-L5.4-W4.0-LS6.5-TR
J11: CONN-TH_XT30PW-M; LCSC_Part_Number C319099
L1: 2.2uH 12.7mOhm C5440776; IND-SMD_L6.6-W6.4_CKSTT0610; LCSC_Part_Number C5440776
R16: 102k; R_0402_1005Metric; LCSC_Part_Number C2933066
R17: 36.5k; R_0402_1005Metric; LCSC_Part_Number C25887
R18: 53.6k; R_0402_1005Metric; LCSC_Part_Number C5153961
R19: 3.92k; R_0402_1005Metric; LCSC_Part_Number C3013164
R24: 53.6k; R_0402_1005Metric; LCSC_Part_Number C2998086
R25: 10k; R_0402_1005Metric; LCSC_Part_Number C2906885
U6: TPS54620RHLR; VQFN-14_L3.5-W3.5-P0.50-TL-EP_TPS54622RHLT; LCSC_Part_Number C263274
U8: AMS1117-3.3; SOT-223-3_TabPin2; LCSC_Part_Number C347222

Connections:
+3.3V: C25.1, U8.2 (VO); also elsewhere on the board
+5V: C24.1, D4.2 (K), U8.3 (VI); also elsewhere on the board
+BATT: C2.1, C15.1, C16.1 (+), C17.1, C19.1, J11.1 (+), R16.1, U6.4 (PVIN), U6.5 (PVIN), U6.6 (VIN); also elsewhere on the board
GND: C1.2, C2.2, C15.2, C16.2 (-), C17.2, C18.2, C19.2, C20.2, C23.2, C24.2, C25.2, J11.2 (-), J11.3, J11.4, R17.2, R18.2, R25.2, U6.2 (GND), U6.3 (GND), U6.15 (EP), U8.1 (GND); also elsewhere on the board
unnamed: C1.1, C20.1, R19.2
unnamed: C22.1, L1.1, U6.11 (PH), U6.12 (PH)
unnamed: C23.1, D4.1 (A), D4.3 (A), L1.2, R24.1
unnamed: C22.2, U6.13 (BOOT)
unnamed: R19.1, U6.8 (COMP)
unnamed: R16.2, R17.1, U6.10 (EN)
unnamed: R18.1, U6.1 (RT/CLK)
unnamed: C18.1, U6.9 (SS/TR)
unnamed: R24.2, R25.1, U6.7 (VSENSE)

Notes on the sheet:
NOTE: According to sims, the switching frequency for this buck will be ~880Khz.
Battery -> 5v rail
Battery Input
5v Rail -> 3v3 Rail

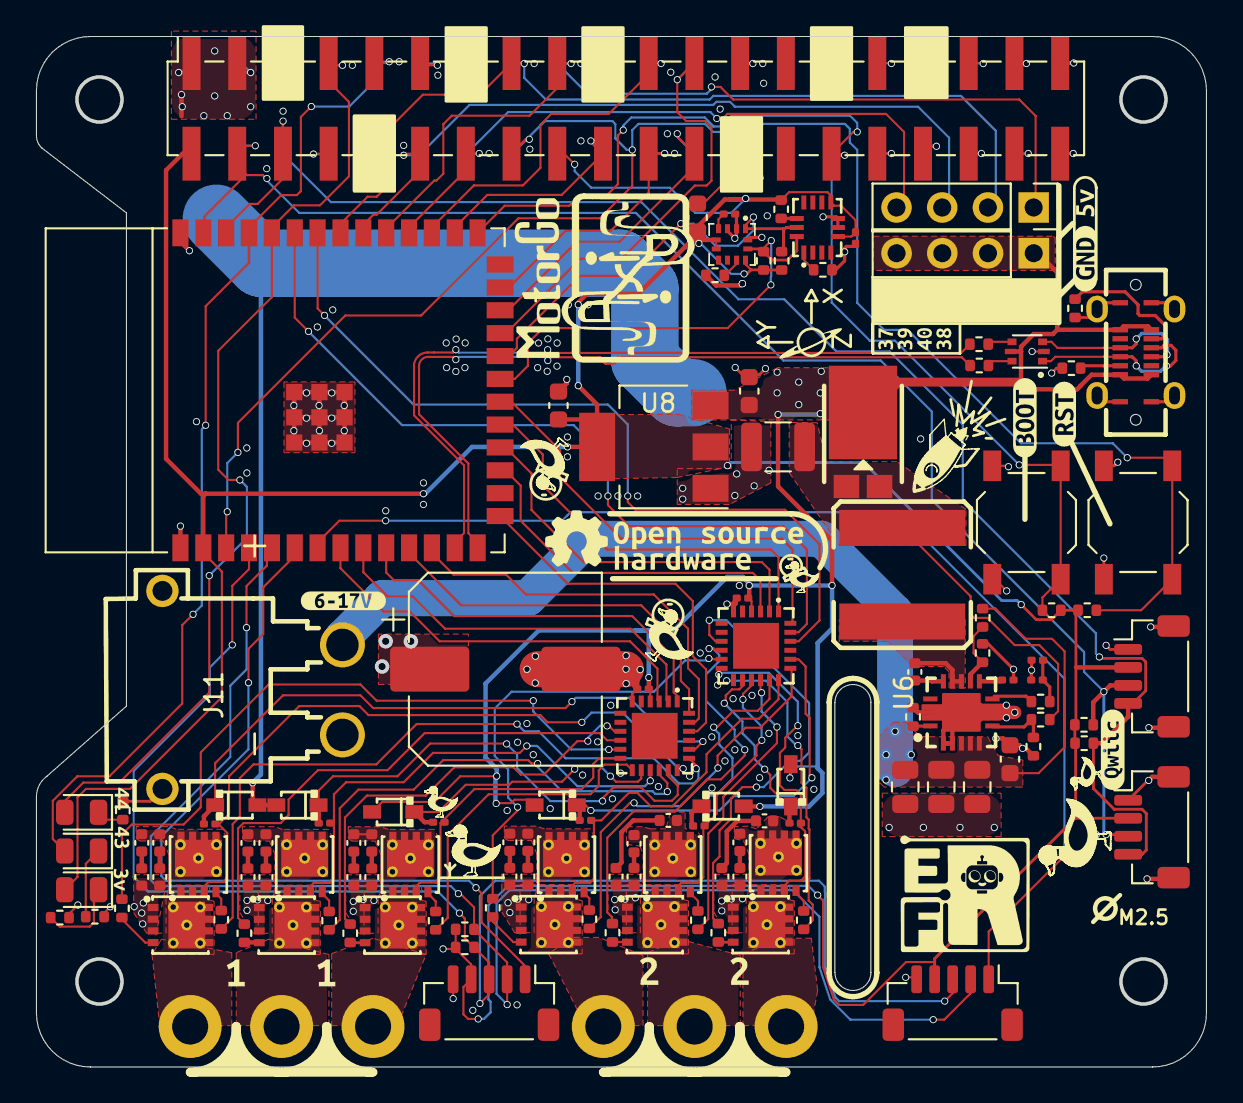
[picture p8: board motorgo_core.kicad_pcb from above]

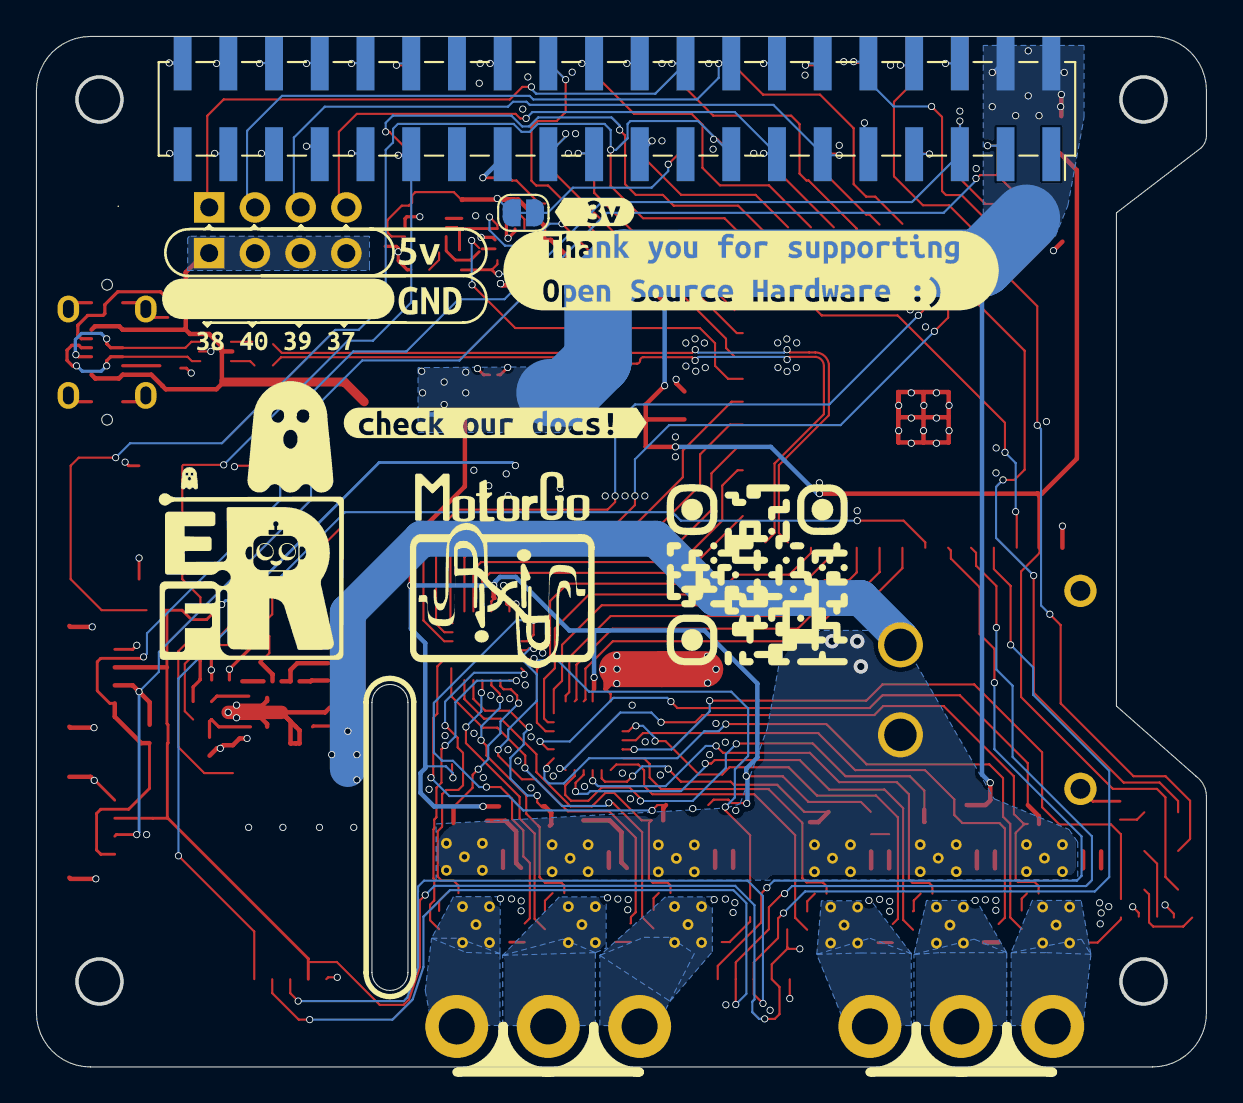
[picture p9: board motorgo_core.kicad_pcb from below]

Board: 4 copper layers, 65.0 x 57.2 mm, 150 parts (7 on the bottom side), 120 nets.

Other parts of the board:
kibuzzard-67A57D3F: G***; kibuzzard-67A57D3F
kibuzzard-670FEBB5: G***; kibuzzard-670FEBB5
kibuzzard-6740A48B: G***; kibuzzard-6740A48B
kibuzzard-6740A353: G***; kibuzzard-6740A353
kibuzzard-6740A543: G***; kibuzzard-6740A543
kibuzzard-6740A668, kibuzzard-6740A668#2: G***; kibuzzard-6740A668
kibuzzard-6740A681, kibuzzard-6740A681#2: G***; kibuzzard-6740A681
kibuzzard-6740AFFF: G***; kibuzzard-6740AFFF
kibuzzard-6740B00B: G***; kibuzzard-6740B00B
kibuzzard-6740B0CA: G***; kibuzzard-6740B0CA
kibuzzard-6740B1FD: G***; kibuzzard-6740B1FD
kibuzzard-6740B03C: G***; kibuzzard-6740B03C
kibuzzard-6740B20C: G***; kibuzzard-6740B20C
kibuzzard-6740E9DD: G***; kibuzzard-6740E9DD
kibuzzard-6740EACA: G***; kibuzzard-6740EACA
kibuzzard-67324B8C: G***; kibuzzard-67324B8C
kibuzzard-67324B68: G***; kibuzzard-67324B68
kibuzzard-67324B83: G***; kibuzzard-67324B83
kibuzzard-673237E1: G***; kibuzzard-673237E1

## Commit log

2024-11-14 initial board design copper layers and components
    [DRV8825.kicad_sch, H_brdige_AP30H80Q.kicad_sch, LISM6.kicad_sch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]
2025-01-04 update to recent production
    [H_brdige_AP30H80Q.kicad_sch, LISM6.kicad_sch, bom.csv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]
2025-02-07 fix polarity of our xt30 connector, add jumper to disconnect 3v rail from pi-header
    [bom.csv, bom_from_jlc.xls, designators.csv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]
2025-02-08 add 3d STEP file of Axis Board
    [mg_axis.step]
